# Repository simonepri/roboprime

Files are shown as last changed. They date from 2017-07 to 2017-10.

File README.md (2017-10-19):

# RoboPrime 🤖 
> Full featured 21 DOF 3D Printed Humanoid Robot based on ATmega328P chip
<p align="center">
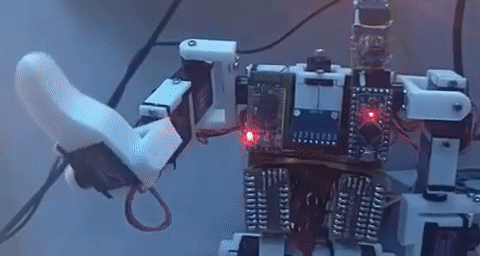
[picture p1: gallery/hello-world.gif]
RoboPrime Hello
  
</p>
Description coming soon.

### Press
The project has been featured here:
<p>
  <a href="http://explore.makerfairerome.eu/poi/Exhibit_1447" target="_blank">Maker Faire</a>
  <a href="http://www.ilmessaggero.it/pay/edicola/maker_faire_roma_14_ottobre-2001501.html" target="_blank"> Il Messagero</a>
</p>

### Gallery
Some images done during the development process:

<p>
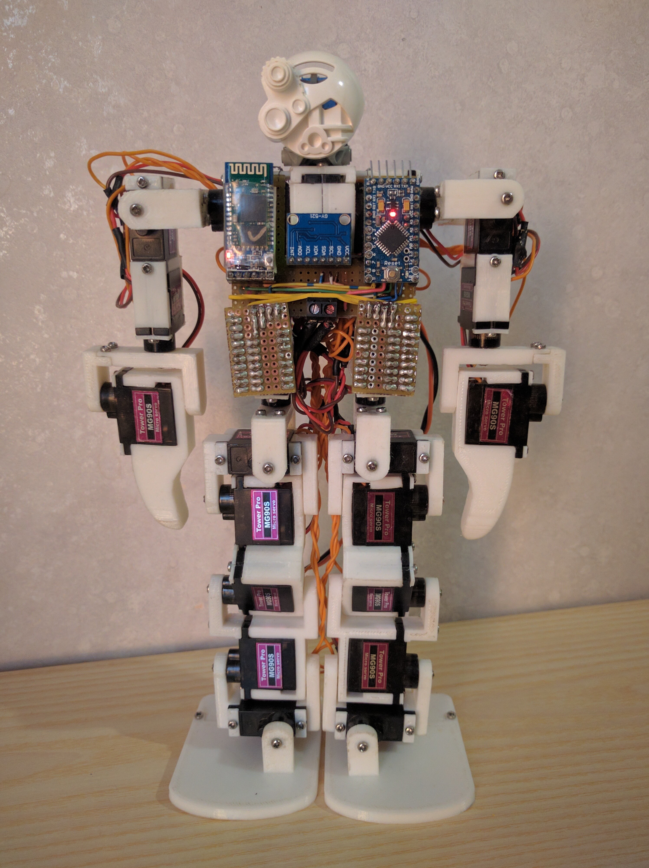
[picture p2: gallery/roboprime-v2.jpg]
RoboPrime
  
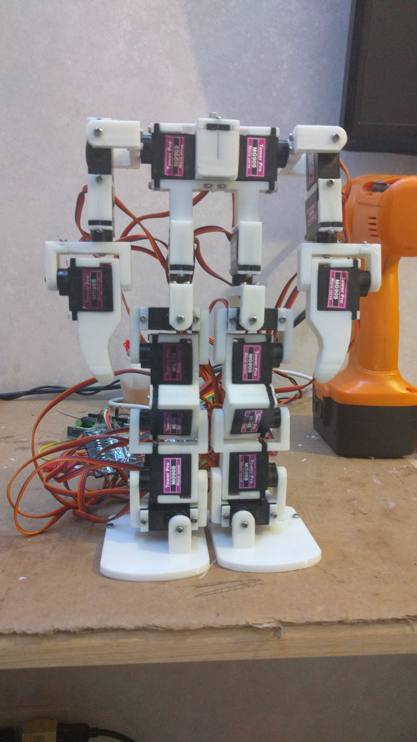
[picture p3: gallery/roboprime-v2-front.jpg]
RoboPrime
  
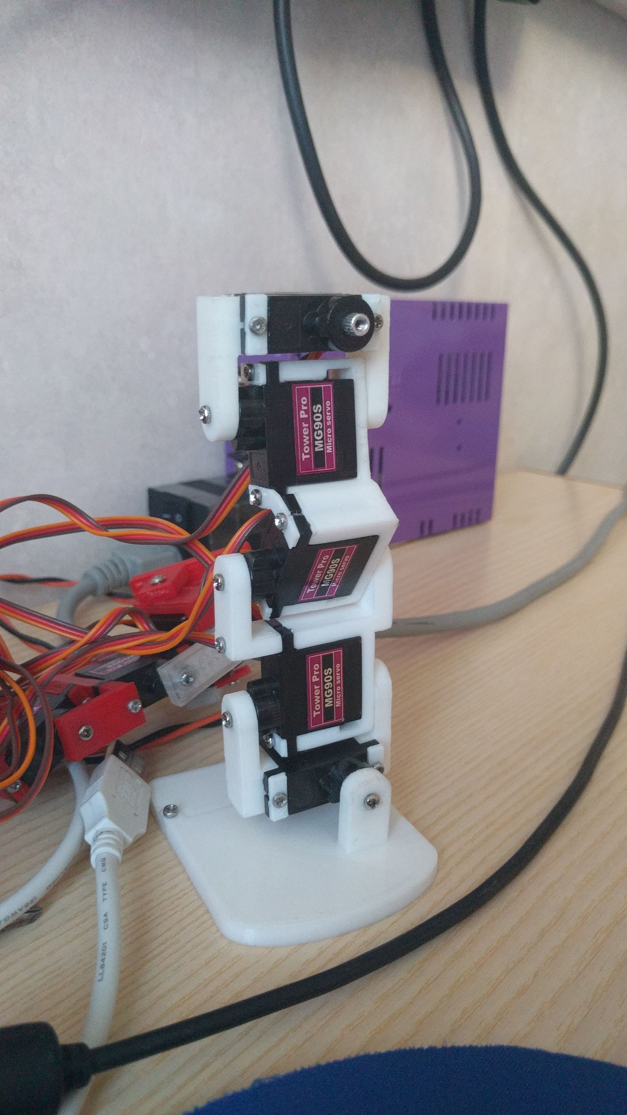
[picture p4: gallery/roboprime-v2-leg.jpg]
RoboPrime
  
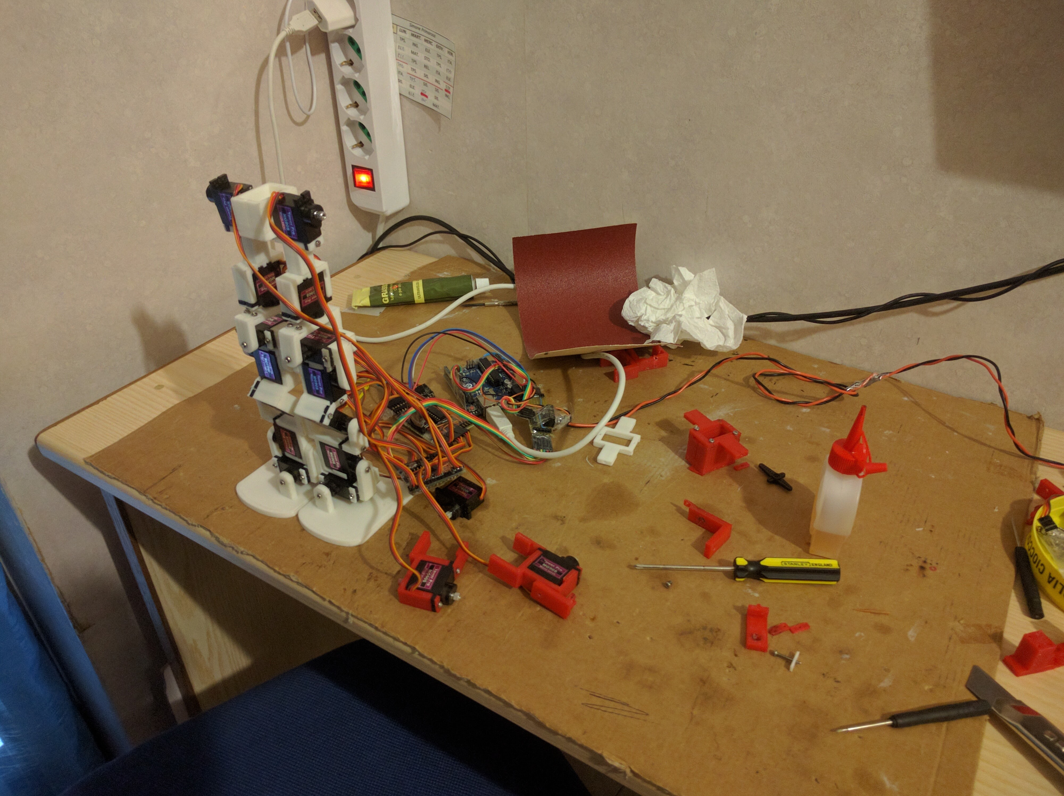
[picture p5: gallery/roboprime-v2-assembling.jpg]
RoboPrime
  
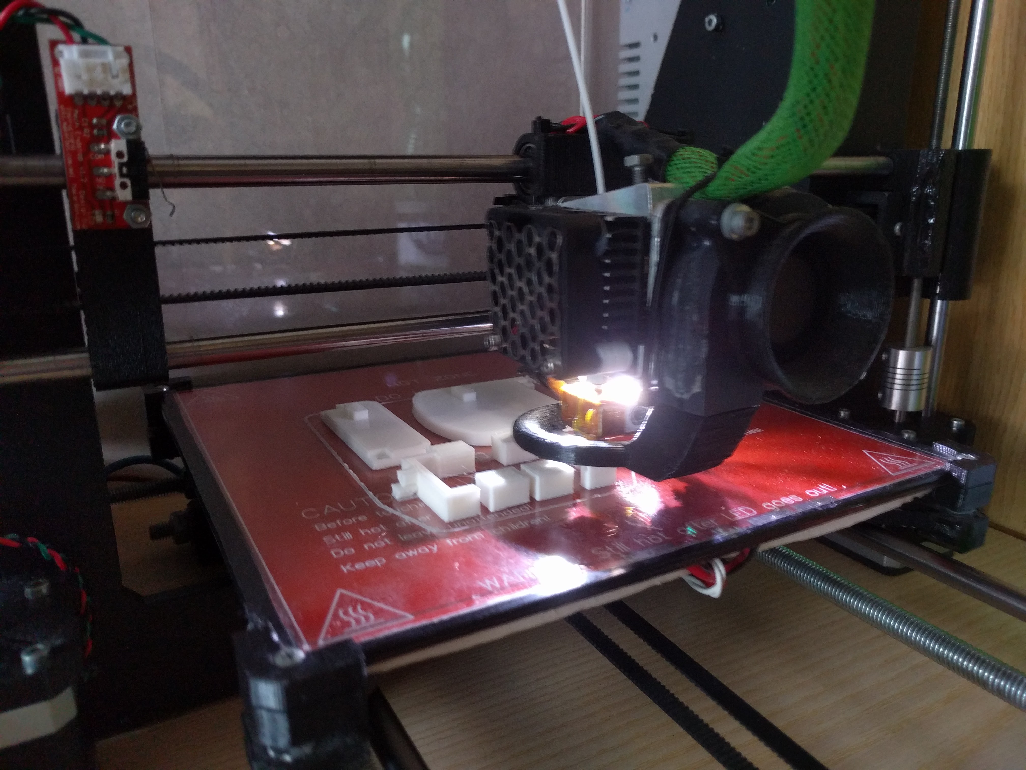
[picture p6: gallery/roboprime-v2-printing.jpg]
RoboPrime
  
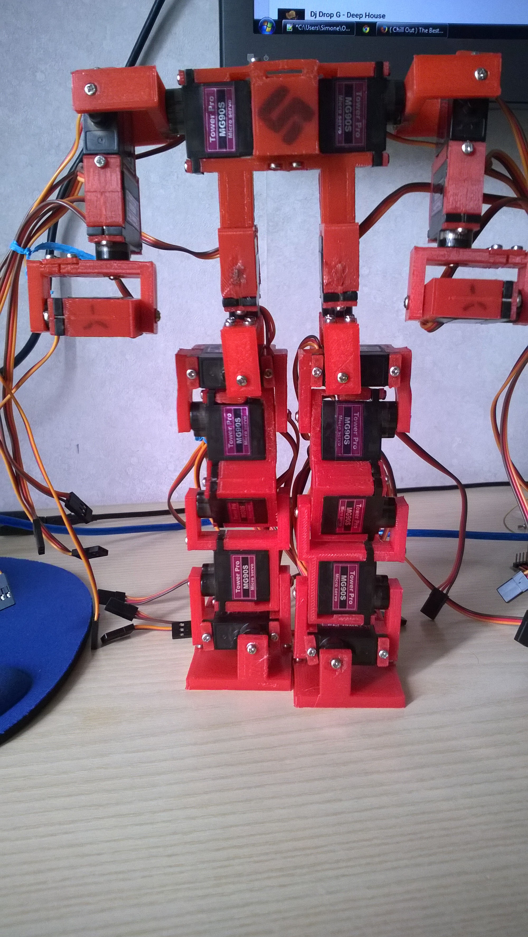
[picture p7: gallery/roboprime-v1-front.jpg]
RoboPrime
  
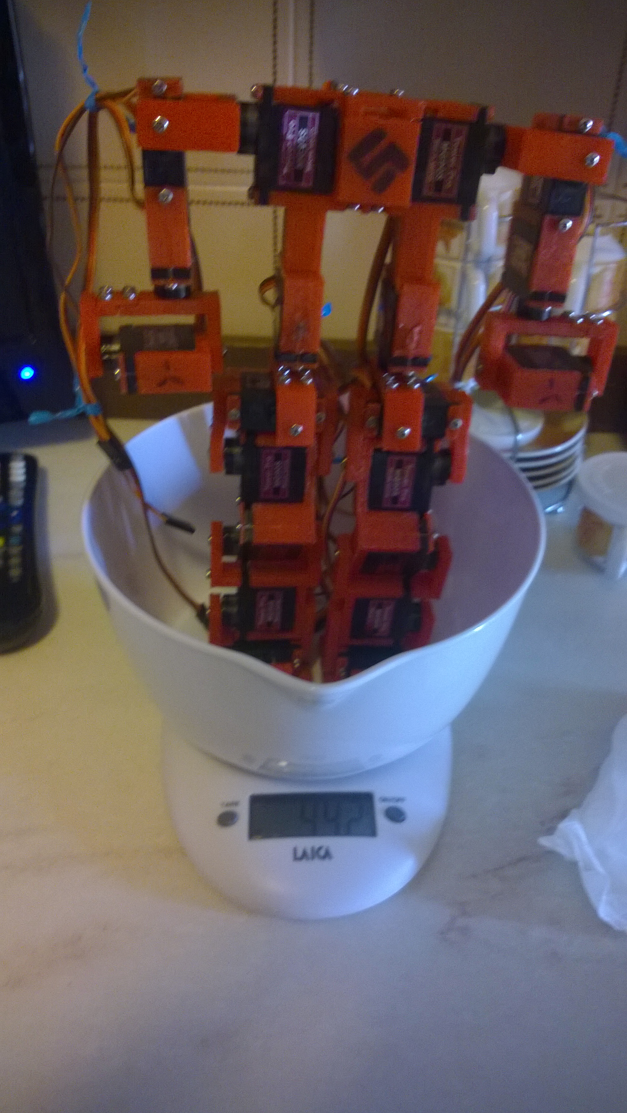
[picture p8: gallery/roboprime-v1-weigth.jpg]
RoboPrime
  
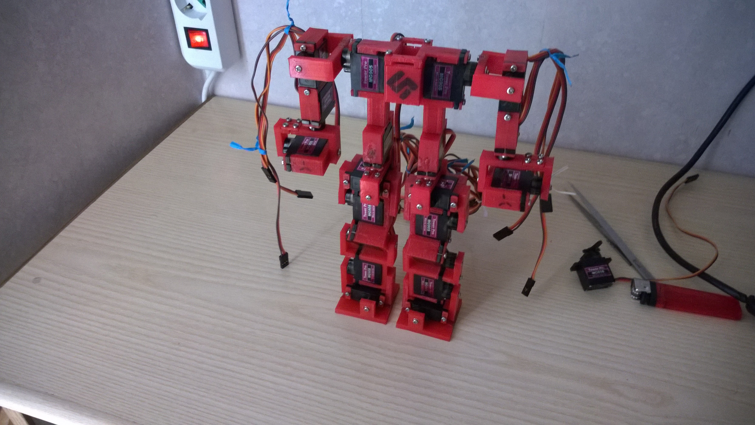
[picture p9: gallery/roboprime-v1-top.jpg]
RoboPrime
  
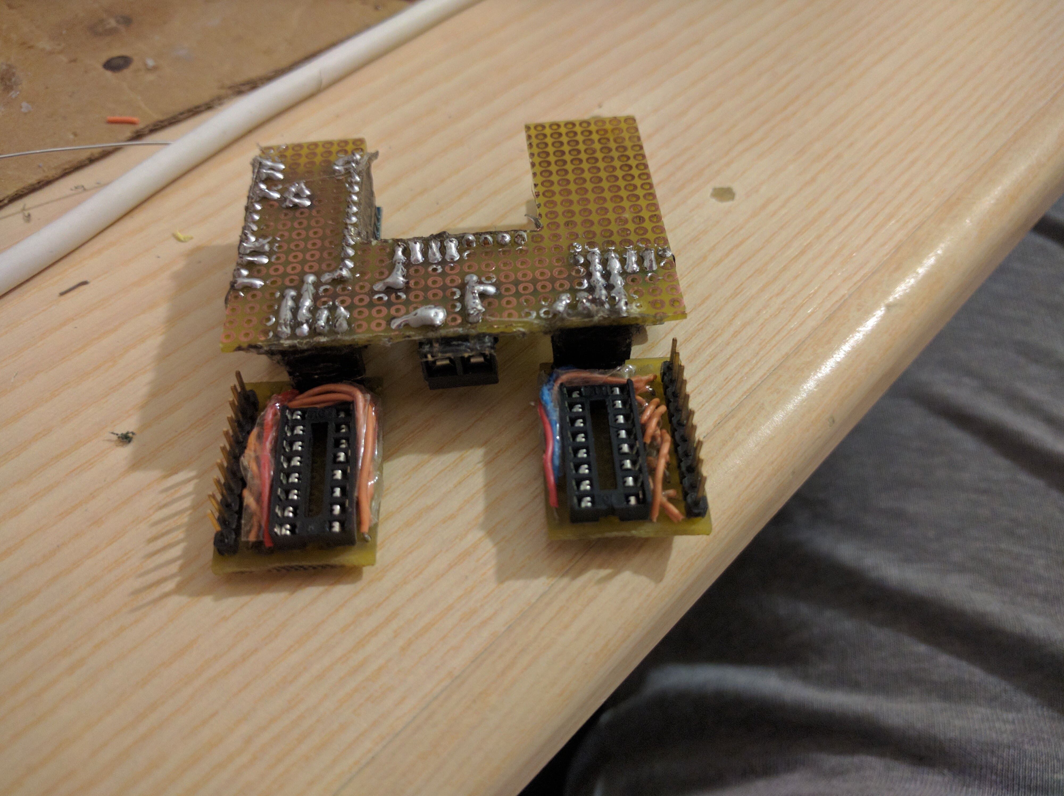
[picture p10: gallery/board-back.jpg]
  
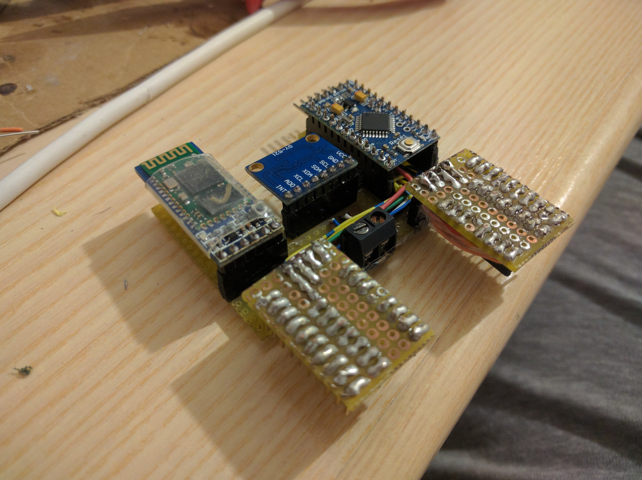
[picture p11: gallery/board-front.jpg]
  
  RoboPrime
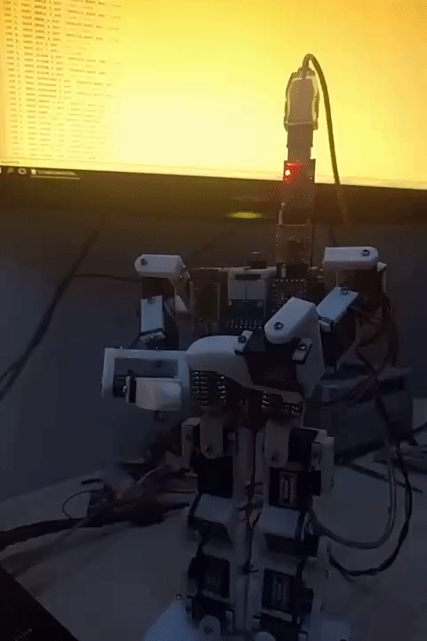
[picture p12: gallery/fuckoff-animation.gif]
  
  RoboPrime
  RoboPrime
</p>

> Click on the image to enlarge.

## Getting Started

### Hardware
The total cost is about $60-$100. Depending on where you buy the pieces.

Amount | Part
-------|---------
1 | Arduino Pro Micro (Atmega328p)
1 | HC-05 (Bluetooth)
2 | 74HC4017 (5-stage Johnson decade counter)
1 | MPU-6050 (Gyroscope + Accellerometer UNUSED)
21 | MG90S 9G (Servo motors)
2 | 5A DC-DC (Voltage step-down Used to power the servos)
1 | Ad-hoc board (See wiring section)

### Screws
Screws are used to join pieces together.

The total cost is about $15.

Amount | Size
-------|------
37 | M2 x 4mm
32 | M2 x 14mm
19 | M2 x 20mm

### 3D Models
You need to print it in ABS, since servos becomes hot after a while and can melt the plastic.

The printing cost is about $20-$30.

> SX_* models needs to be mirrored on the correct axis before the printing process.

Part | Amount | Download
-----|--------|---------
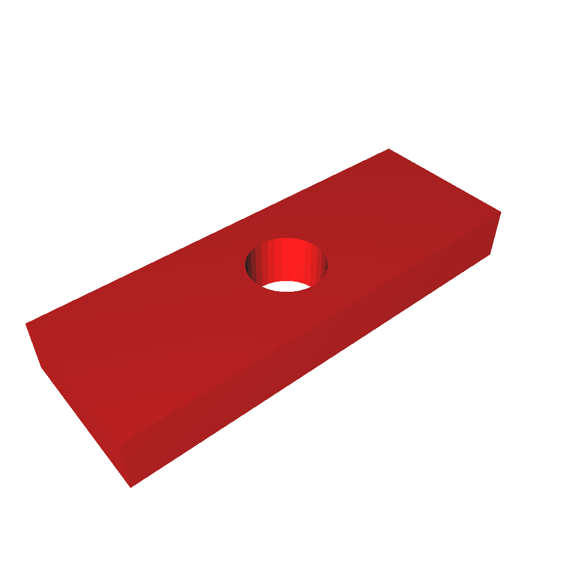
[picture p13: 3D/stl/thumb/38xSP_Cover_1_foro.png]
SP_Cover_1_foro
 | 38 | [SP_Cover_1_foro](3D/stl/38xSP_Cover_1_foro.stl)
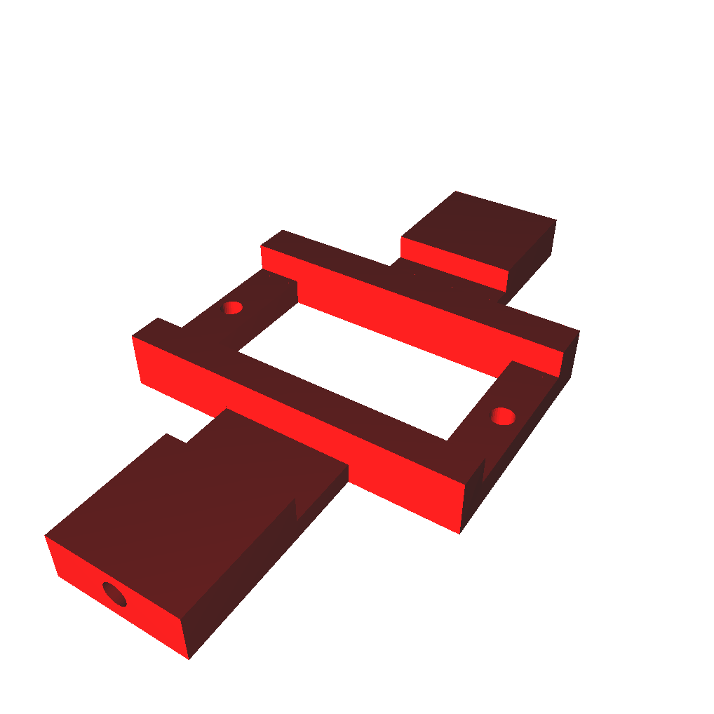
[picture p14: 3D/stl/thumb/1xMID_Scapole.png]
MID_Scapole
 | 1 | [MID_Scapole](3D/stl/1xMID_Scapole.stl)
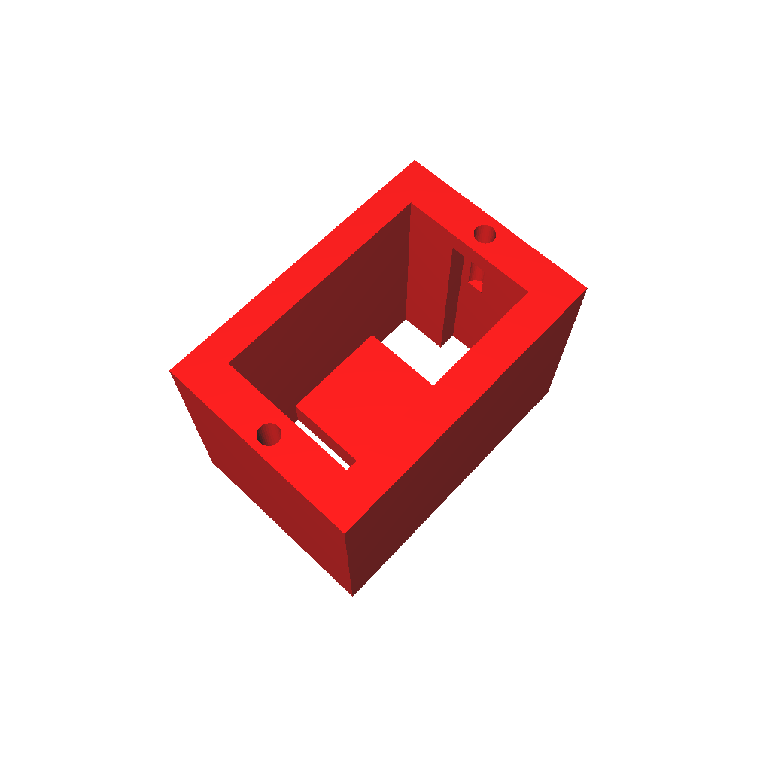
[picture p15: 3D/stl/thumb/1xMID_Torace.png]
MID_Torace
 | 1 | [MID_Torace](3D/stl/1xMID_Torace.stl)
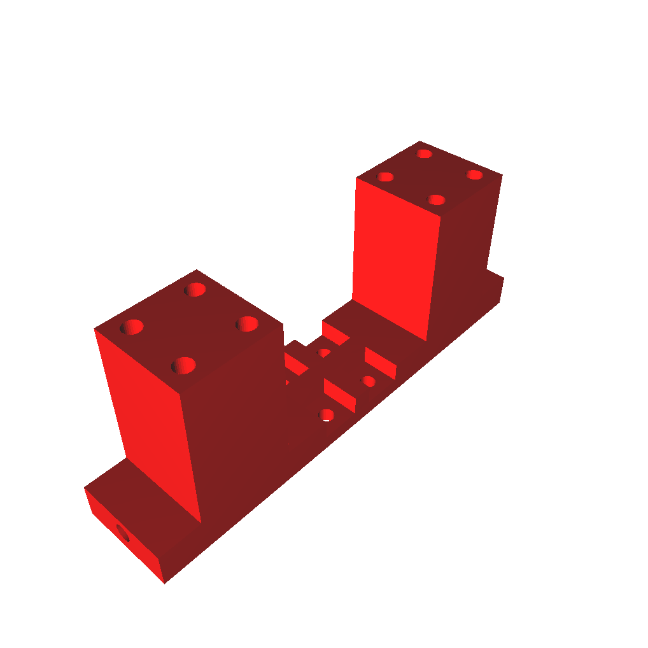
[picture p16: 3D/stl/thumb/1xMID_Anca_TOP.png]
MID_Anca_TOP
 | 1 | [MID_Anca_TOP](3D/stl/1xMID_Anca_TOP.stl)
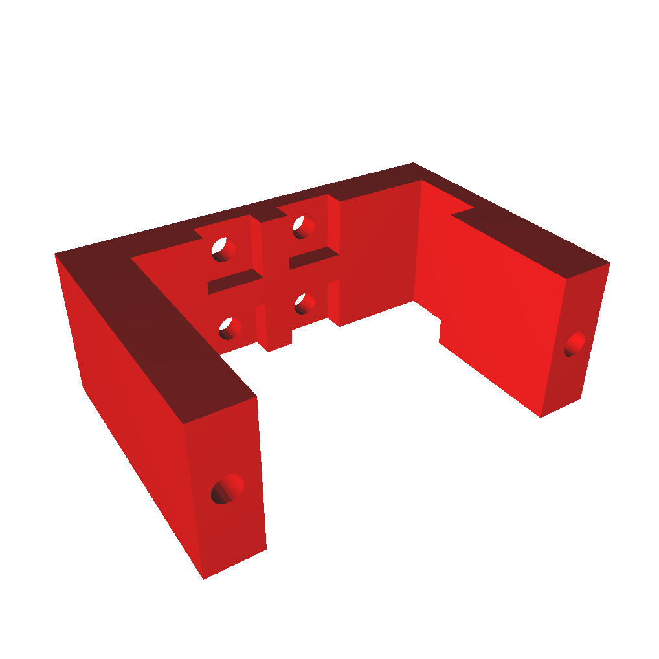
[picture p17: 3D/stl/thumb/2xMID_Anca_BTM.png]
MID_Anca_BTM
 | 2 | [MID_Anca_BTM](3D/stl/2xMID_Anca_BTM.stl)
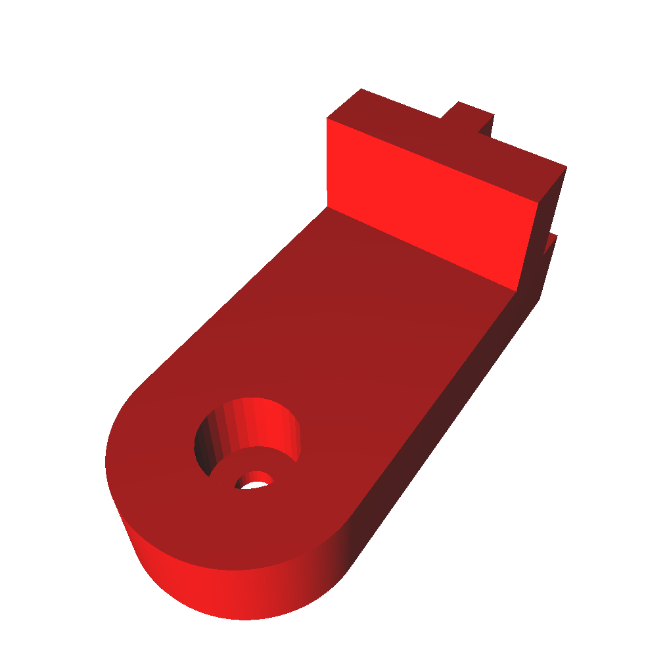
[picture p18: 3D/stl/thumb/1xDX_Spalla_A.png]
DX_Spalla_A
 | 1 | [DX_Spalla_A](3D/stl/1xDX_Spalla_A.stl)
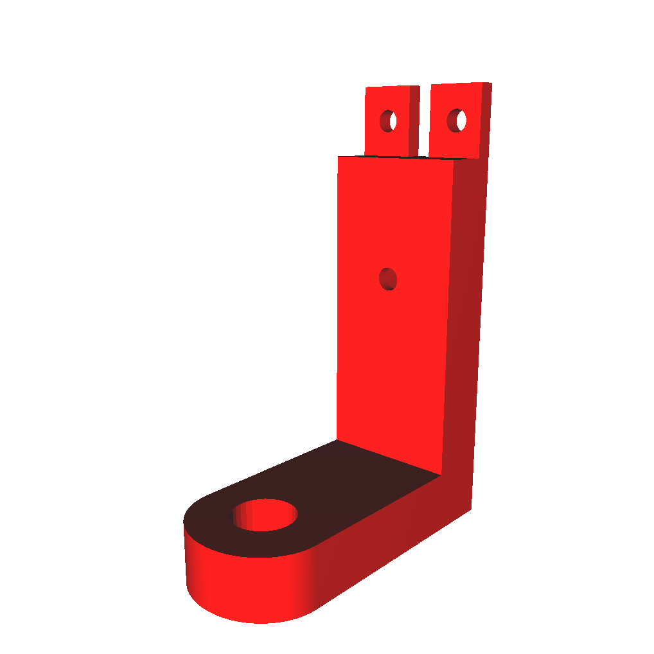
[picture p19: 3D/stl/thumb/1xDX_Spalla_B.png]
DX_Spalla_B
 | 1 | [DX_Spalla_B](3D/stl/1xDX_Spalla_B.stl)
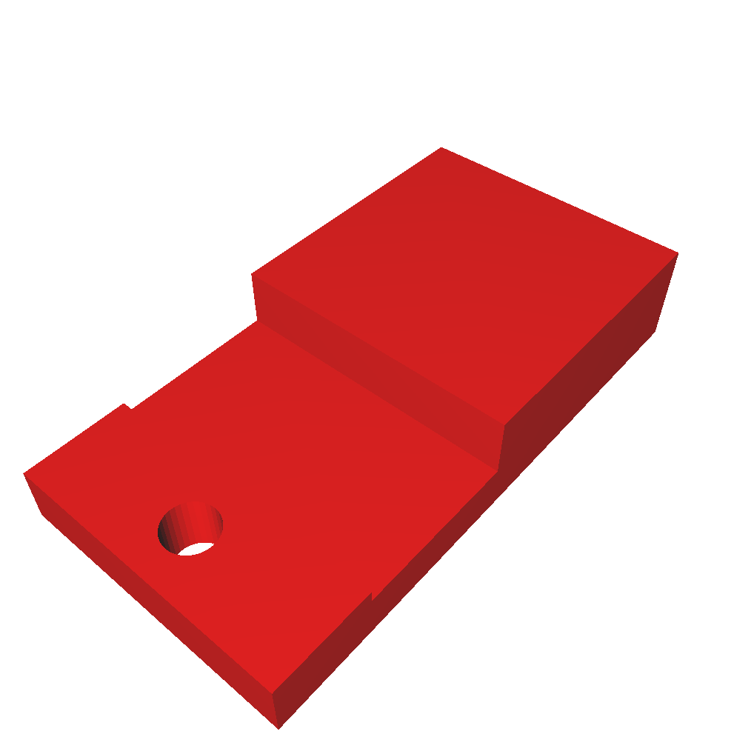
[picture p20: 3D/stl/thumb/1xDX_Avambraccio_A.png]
DX_Avambraccio_A
 | 1 | [DX_Avambraccio_A](3D/stl/1xDX_Avambraccio_A.stl)
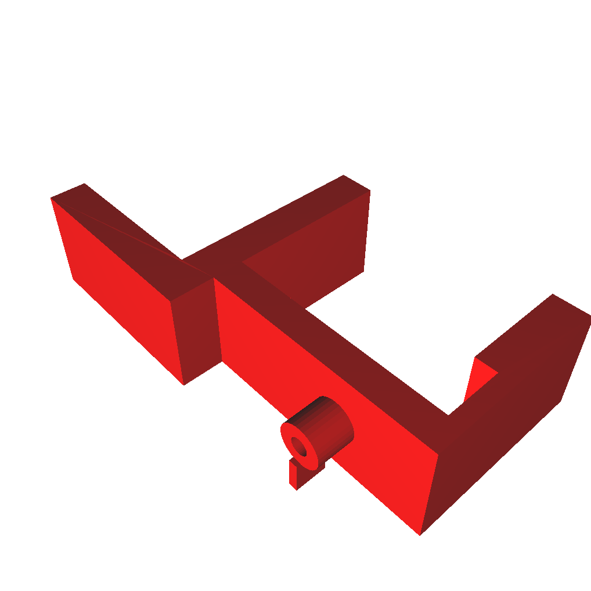
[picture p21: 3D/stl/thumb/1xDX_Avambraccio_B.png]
DX_Avambraccio_B
 | 1 | [DX_Avambraccio_B](3D/stl/1xDX_Avambraccio_B.stl)
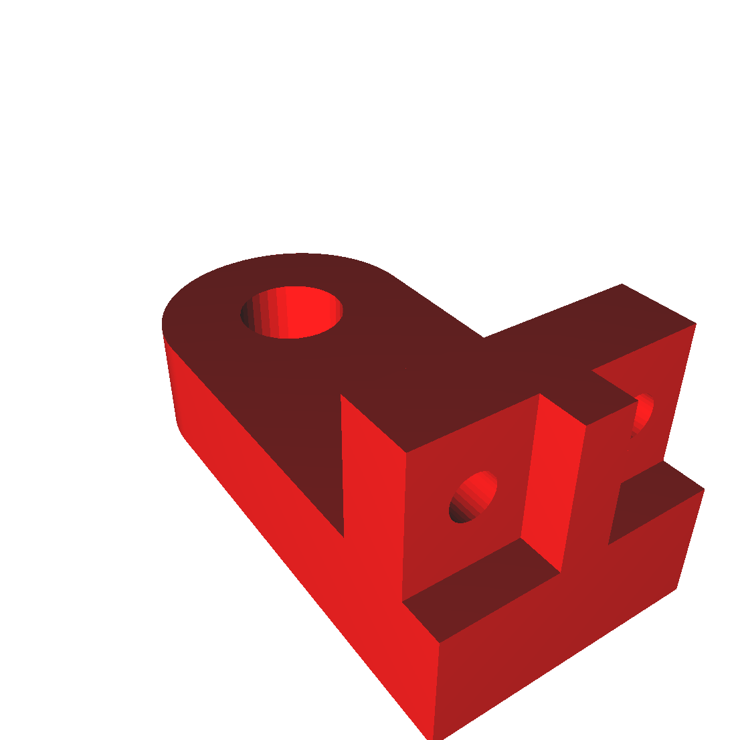
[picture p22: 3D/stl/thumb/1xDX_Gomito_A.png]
DX_Gomito_A
 | 1 | [DX_Gomito_A](3D/stl/1xDX_Gomito_A.stl)
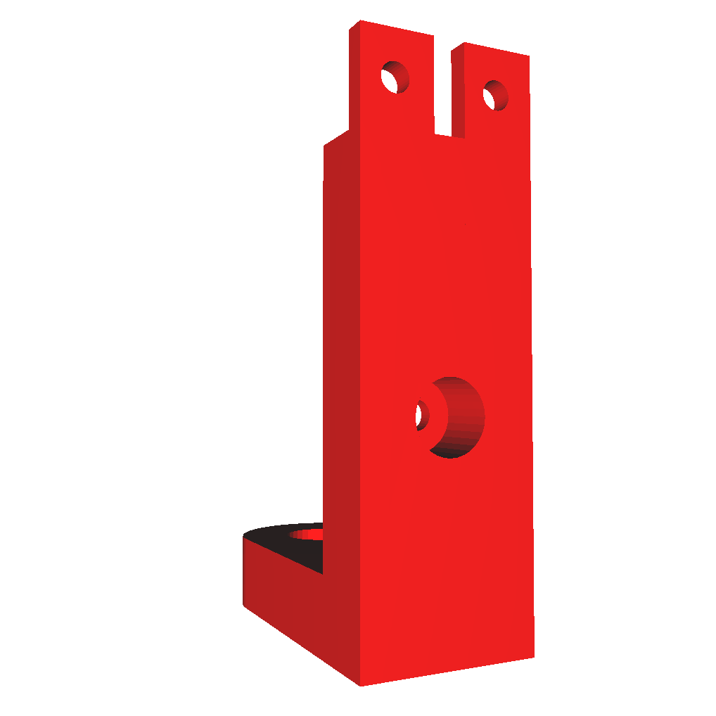
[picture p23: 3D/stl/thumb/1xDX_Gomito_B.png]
DX_Gomito_B
 | 1 | [DX_Gomito_B](3D/stl/1xDX_Gomito_B.stl)
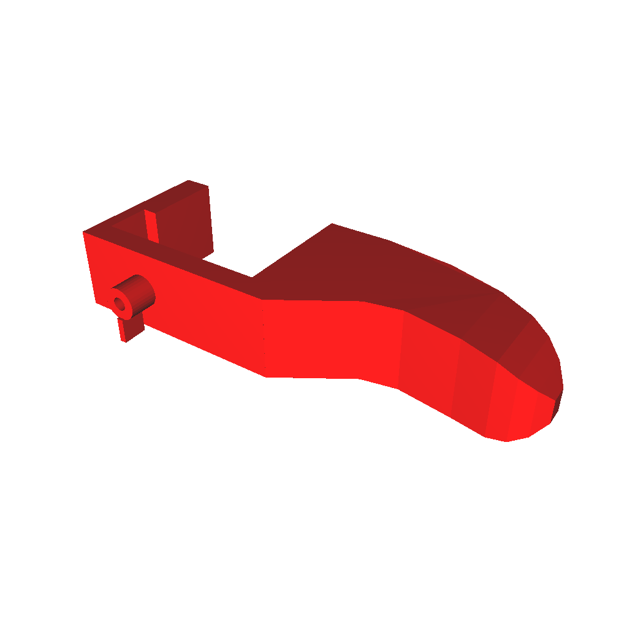
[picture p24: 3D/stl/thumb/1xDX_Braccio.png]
DX_Braccio
 | 1 | [DX_Braccio](3D/stl/1xDX_Braccio.stl)
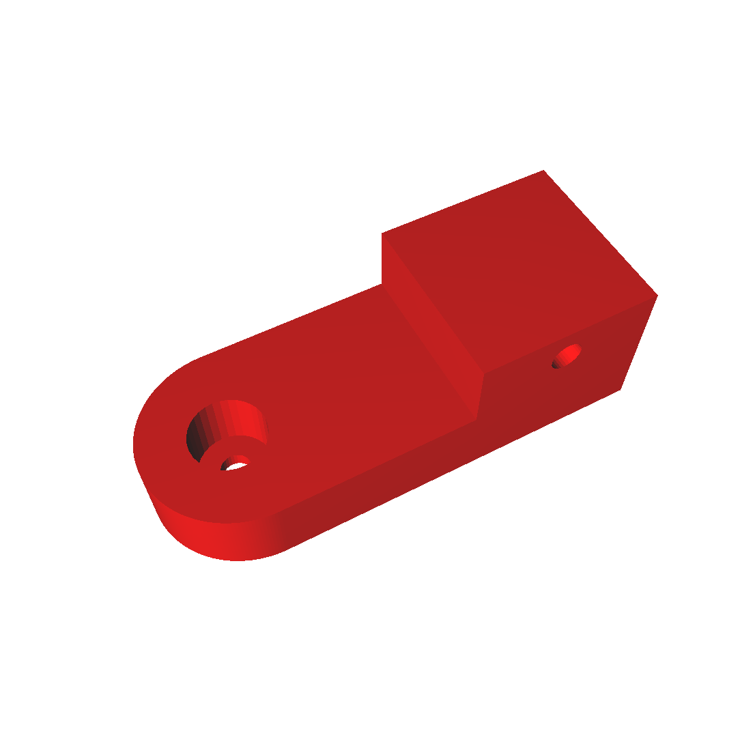
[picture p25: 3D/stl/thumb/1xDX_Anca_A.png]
DX_Anca_A
 | 1 | [DX_Anca_A](3D/stl/1xDX_Anca_A.stl)
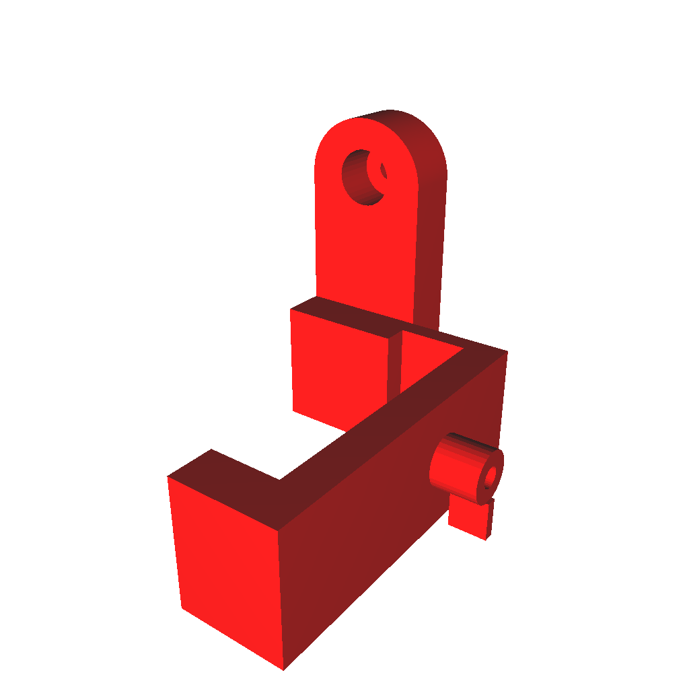
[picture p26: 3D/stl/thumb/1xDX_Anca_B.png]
DX_Anca_B
 | 1 | [DX_Anca_B](3D/stl/1xDX_Anca_B.stl)
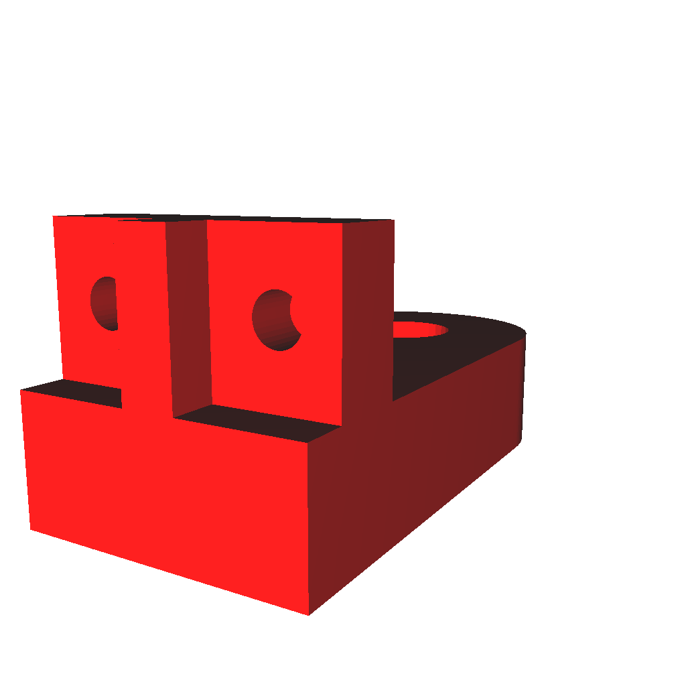
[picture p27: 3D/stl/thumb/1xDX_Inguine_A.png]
DX_Inguine_A
 | 1 | [DX_Inguine_A](3D/stl/1xDX_Inguine_A.stl)
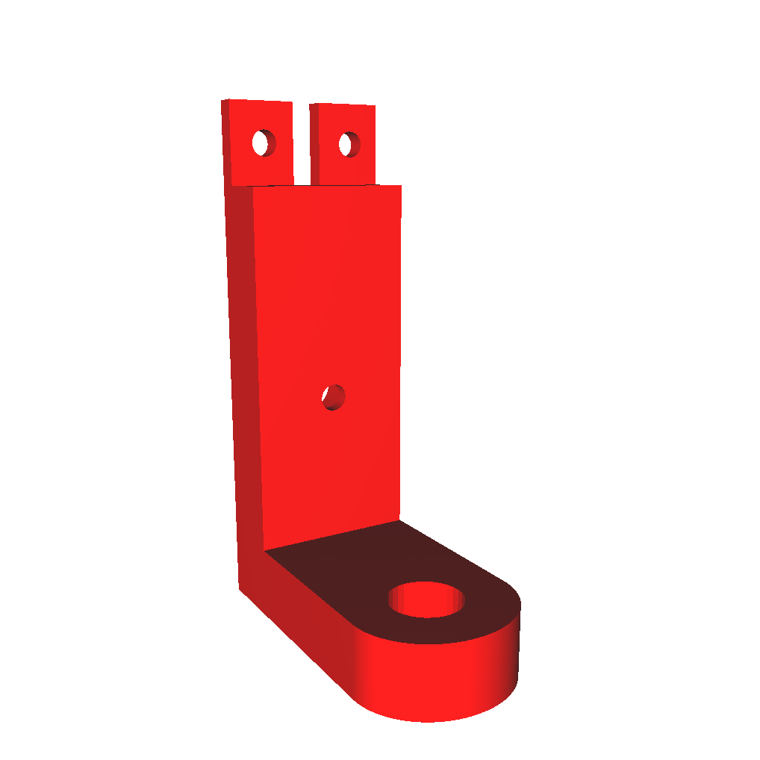
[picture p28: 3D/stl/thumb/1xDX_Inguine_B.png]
DX_Inguine_B
 | 1 | [DX_Inguine_B](3D/stl/1xDX_Inguine_B.stl)
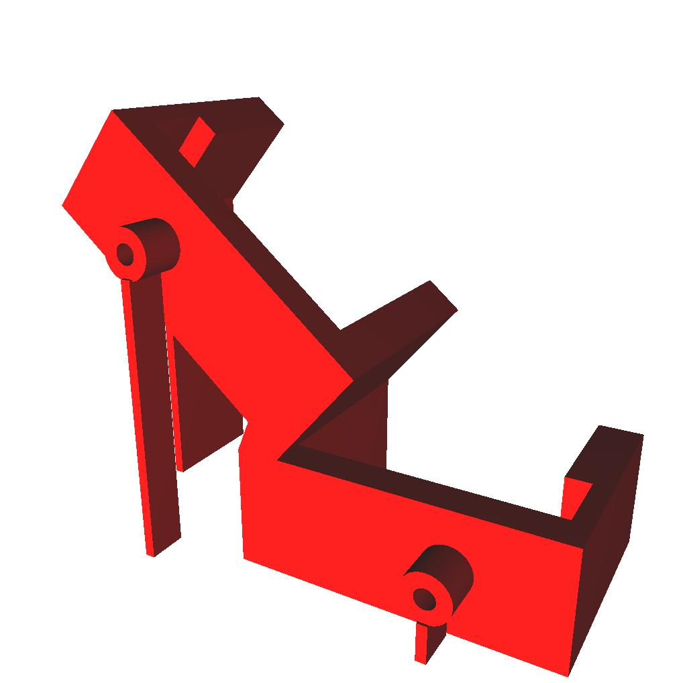
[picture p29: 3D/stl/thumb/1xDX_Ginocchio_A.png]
DX_Ginocchio_A
 | 1 | [DX_Ginocchio_A](3D/stl/1xDX_Ginocchio_A.stl)
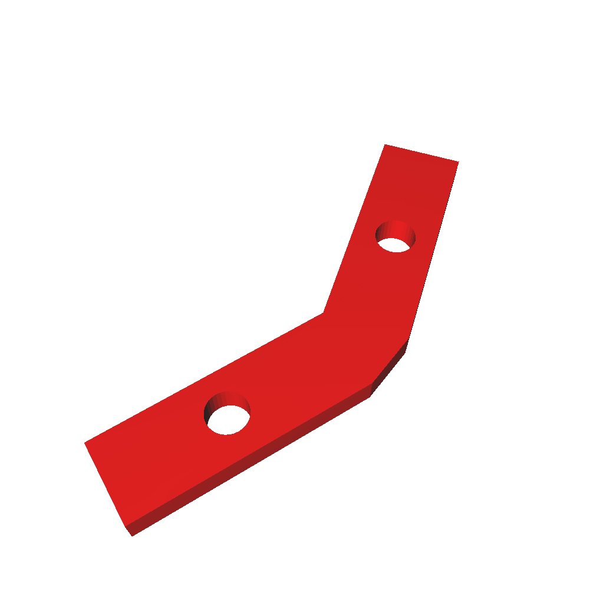
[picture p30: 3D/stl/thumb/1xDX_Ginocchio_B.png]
DX_Ginocchio_B
 | 1 | [DX_Ginocchio_B](3D/stl/1xDX_Ginocchio_B.stl)
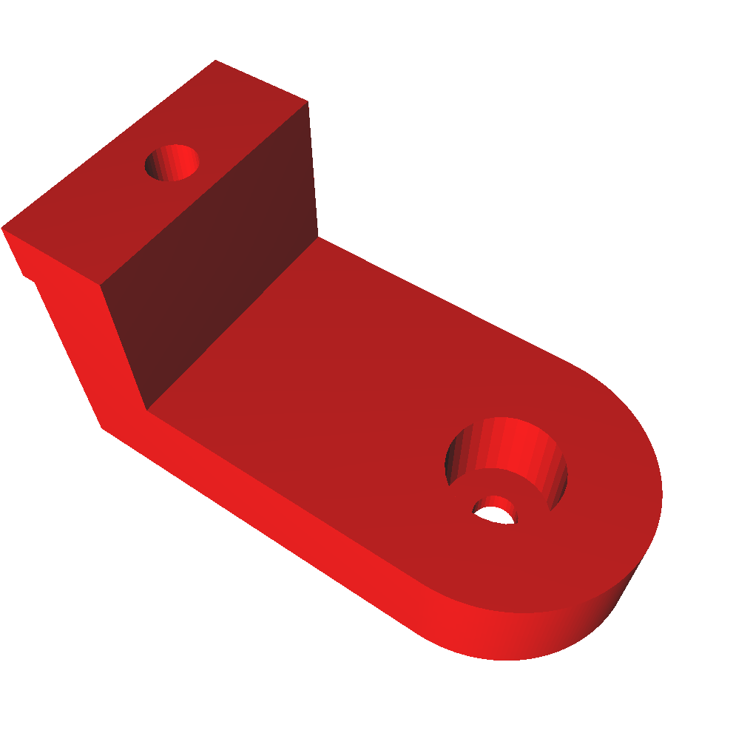
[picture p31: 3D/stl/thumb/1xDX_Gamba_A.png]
DX_Gamba_A
 | 1 | [DX_Gamba_A](3D/stl/1xDX_Gamba_A.stl)
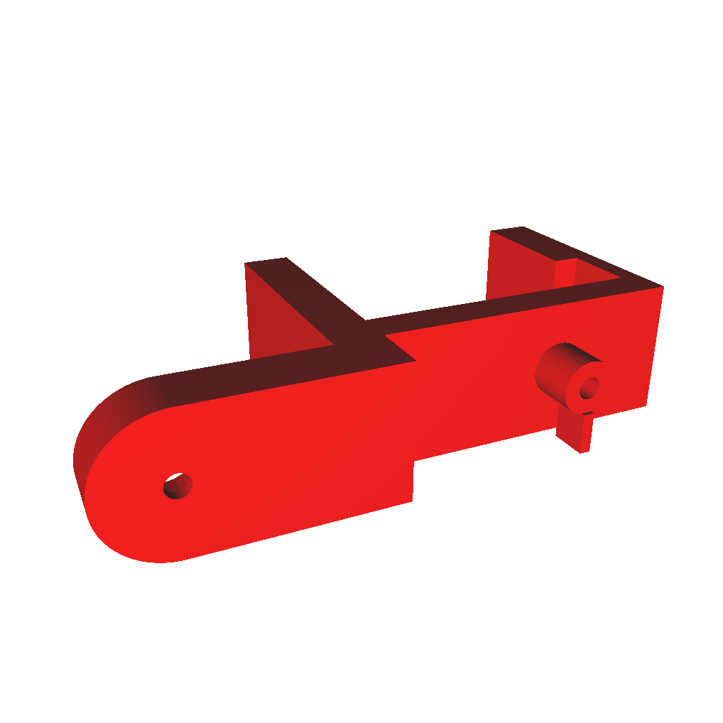
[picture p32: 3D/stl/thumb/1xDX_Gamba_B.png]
DX_Gamba_B
 | 1 | [DX_Gamba_B](3D/stl/1xDX_Gamba_B.stl)
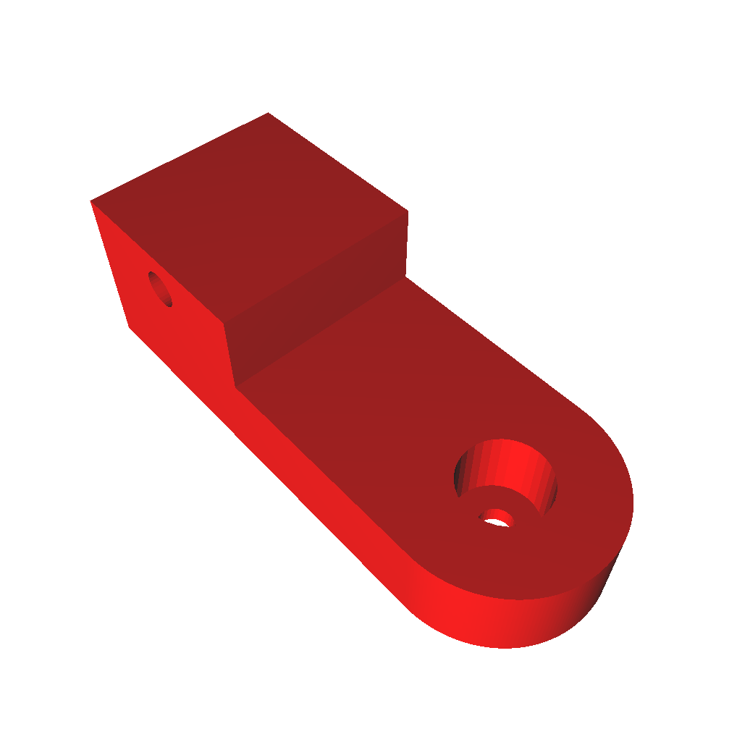
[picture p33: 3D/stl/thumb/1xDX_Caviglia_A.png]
DX_Caviglia_A
 | 1 | [DX_Caviglia_A](3D/stl/1xDX_Caviglia_A.stl)
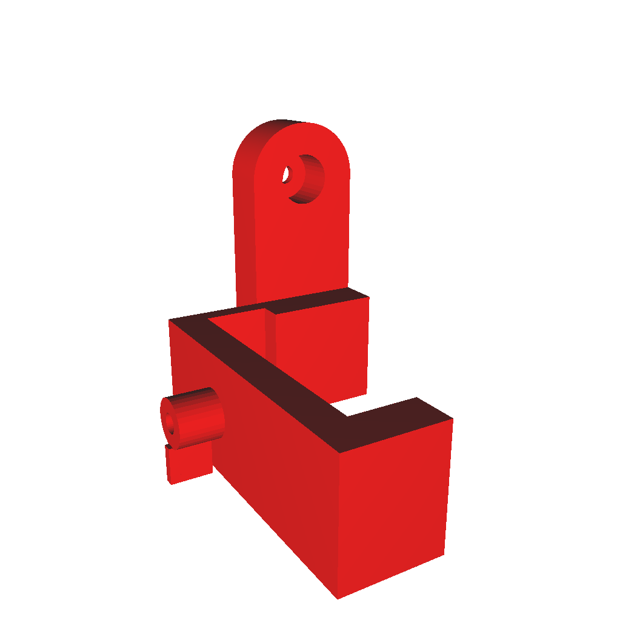
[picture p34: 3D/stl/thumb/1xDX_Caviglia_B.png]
DX_Caviglia_B
 | 1 | [DX_Caviglia_B](3D/stl/1xDX_Caviglia_B.stl)
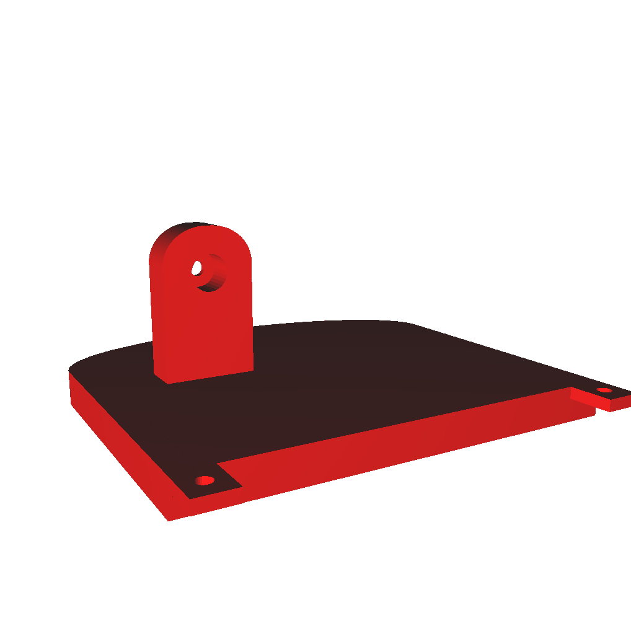
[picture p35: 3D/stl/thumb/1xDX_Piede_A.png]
DX_Piede_A
 | 1 | [DX_Piede_A](3D/stl/1xDX_Piede_A.stl)
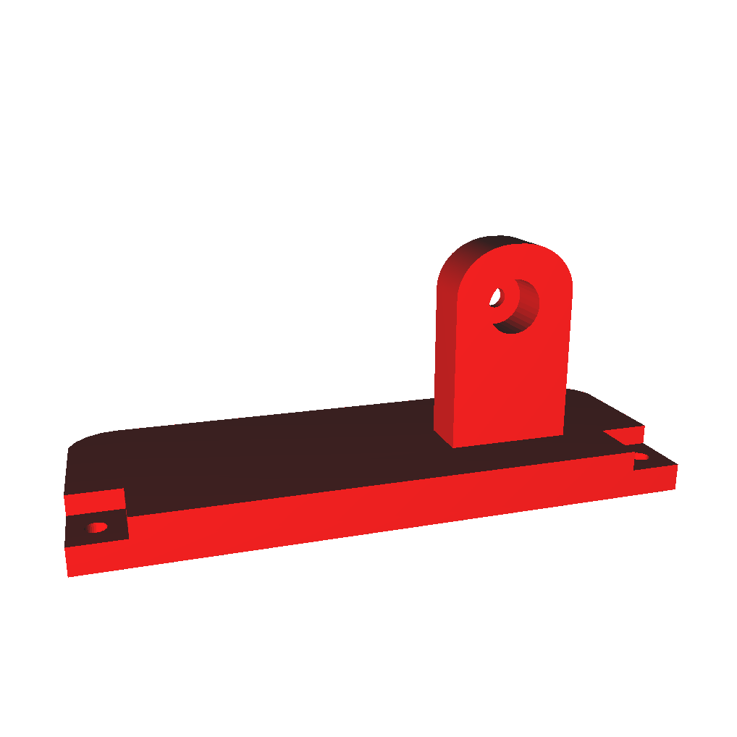
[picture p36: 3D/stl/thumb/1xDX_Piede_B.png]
DX_Piede_B
 | 1 | [DX_Piede_B](3D/stl/1xDX_Piede_B.stl)
SX_Spalla_A | 1 | [SX_Spalla_A](3D/stl/1xDX_Spalla_A.stl)
SX_Spalla_B | 1 | [SX_Spalla_B](3D/stl/1xDX_Spalla_B.stl)
SX_Avambraccio_A | 1 | [SX_Avambraccio_A](3D/stl/1xDX_Avambraccio_A.stl)
SX_Avambraccio_B | 1 | [SX_Avambraccio_B](3D/stl/1xDX_Avambraccio_B.stl)
SX_Gomito_A | 1 | [SX_Gomito_A](3D/stl/1xDX_Gomito_A.stl)
SX_Gomito_B | 1 | [SX_Gomito_B](3D/stl/1xDX_Gomito_B.stl)
SX_Braccio | 1 | [SX_Braccio](3D/stl/1xDX_Braccio.stl)
SX_Anca_A | 1 | [SX_Anca_A](3D/stl/1xDX_Anca_A.stl)
SX_Anca_B | 1 | [SX_Anca_B](3D/stl/1xDX_Anca_B.stl)
SX_Inguine_A | 1 | [SX_Inguine_A](3D/stl/1xDX_Inguine_A.stl)
SX_Inguine_B | 1 | [SX_Inguine_B](3D/stl/1xDX_Inguine_B.stl)
SX_Ginocchio_A | 1 | [SX_Ginocchio_A](3D/stl/1xDX_Ginocchio_A.stl)
SX_Ginocchio_B | 1 | [SX_Ginocchio_B](3D/stl/1xDX_Ginocchio_B.stl)
SX_Gamba_A | 1 | [SX_Gamba_A](3D/stl/1xDX_Gamba_A.stl)
SX_Gamba_B | 1 | [SX_Gamba_B](3D/stl/1xDX_Gamba_B.stl)
SX_Caviglia_A | 1 | [SX_Caviglia_A](3D/stl/1xDX_Caviglia_A.stl)
SX_Caviglia_B | 1 | [SX_Caviglia_B](3D/stl/1xDX_Caviglia_B.stl)
SX_Piede_A | 1 | [SX_Piede_A](3D/stl/1xDX_Piede_A.stl)
SX_Piede_B | 1 | [SX_Piede_B](3D/stl/1xDX_Piede_B.stl)

### Wiring
Schematics are contained in the `schematics` folder.
RoboPrime fritzing

### Firmware
The firmware is contained in the `firmware` folder and can be compiled and uploaded to the board thanks to the Arduino IDE.

Firmware size

## Usage

### Commands
The firmware allows you to fully control the robot through bluetooth in order to make complex things.
Those are the commands implemented that can be sended through the serial protocol.

Name | Syntax | Parameters | Description
-----|--------|------------|------------
S0 | `S0 Ri`<br>or<br>`S0 Li` | **i** = index[0-9] (optional) | Move a servo to its default position.<br>If no index is passed all servos will be reset.
S1 | `S1 Ri Ad`<br>or<br>`S1 Li Ad` | **i** = index[0-9]<br>**d** = angle[0-1800] | Move a servo to a specific angle.<br>The value 0 corresponds to 0° and <br>the value 1800 corresponds to 180°.
S2 | `S1 Ri Ad Tm`<br>or<br>`S1 Li Ad Tm` | **i** = index[0-9]<br>**d** = angle[0-1800]<br>**m** = duration[ms] | Move a servo to a specific angle gradually by <br>sweeping it for a specific amount of time.
S3 | `S3 An Ds Tm` | **n** = anim idx[0-10]<br>**s** = space[cm]<br>**m** = duration[ms] | Apply a specific animation.<br>`space` and `duration` are unused at the moment <br>but are supposed to be used as parameters for <br>certain animations. See animations section for <br>the list of animations available.
Q0 | `Q0 Ri Ad`<br>or<br>`Q0 Ri Ad` | **i** = index[0-9]<br>**d** = angle[0-1800] | Similar to `S1`, but the movement is added to <br>the movements queue. If the angle value is 0 <br>a pause will be planned instead.<br>(A pause will make the next planned <br>movement, on the same motor index, hang until <br>the pause is not ended)<br>This is used in order to plan complex <br>synchronized movements. (E.g. Animations)
C0 | `Ri Wp`<br>or<br>`Li Wp` | **i** = index[0-9]<br>**p** = pulse width[us] | Sets a specific pulse width to a specific <br>motor for calibration purposes.

### Animations

The firmware contains some basic animations hardcoded inside it:

Id | Name | Status
---|------|-------
0  | Forward walk.                         | WIP
1  | Backward walk.                        | NO
2  | Side walk to right.                   | NO
3  | Side walk to left.                    | NO
4  | Clockwise standstill rotation.        | NO
5  | Counterclockwise standstill rotation. | NO
6  | Clockwise curved walk.                | NO
7  | Counterclockwise curved walk.         | NO
8  | Sit down.                             | DONE
9  | Hello.                                | DONE
10 | Fuck off.                             | DONE

## Project Analysis
This document was written for my high-school exam in order to give to the professors some basic knowledge to make them understand how the project works.

Unfortunately it's written in Italian 🇮🇹

[The document is available here](https://goo.gl/ZiD9bK)

## Authors
* **Simone Primarosa** - [simonepri](https://github.com/simonepri)

See also the list of [contributors](https://github.com/simonepri/roboprime/contributors) who participated in this project.

## License
This project is licensed under the GPL-3.0 License - see the [LICENSE](LICENSE) file for details.

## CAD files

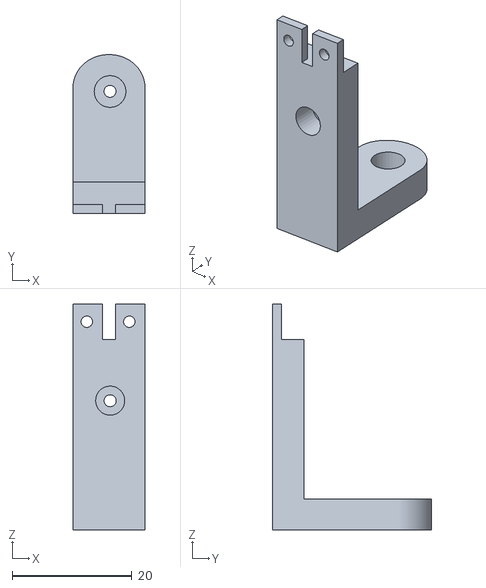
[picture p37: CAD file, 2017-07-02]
3D/stl/1xDX_Spalla_B.stl
12.0 x 26.5 x 37.7

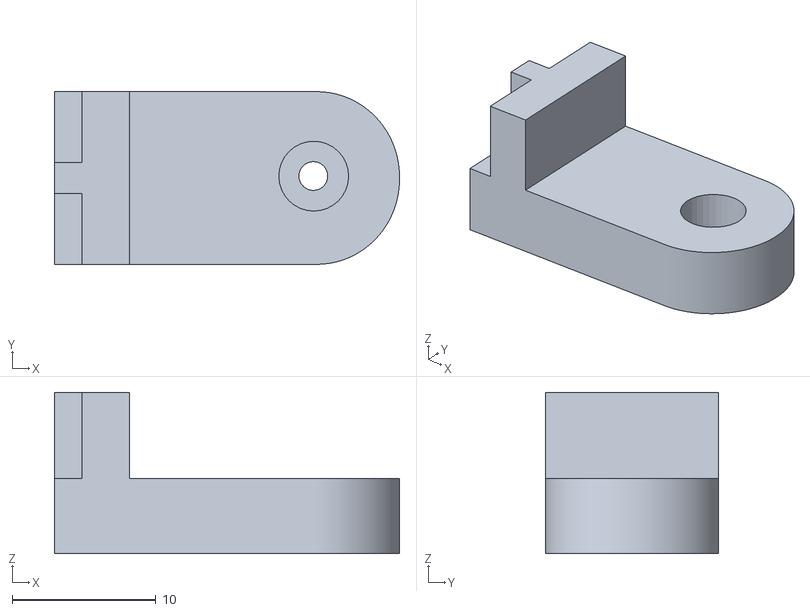
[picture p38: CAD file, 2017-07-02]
3D/stl/1xDX_Inguine_A.stl
24.0 x 12.0 x 11.2

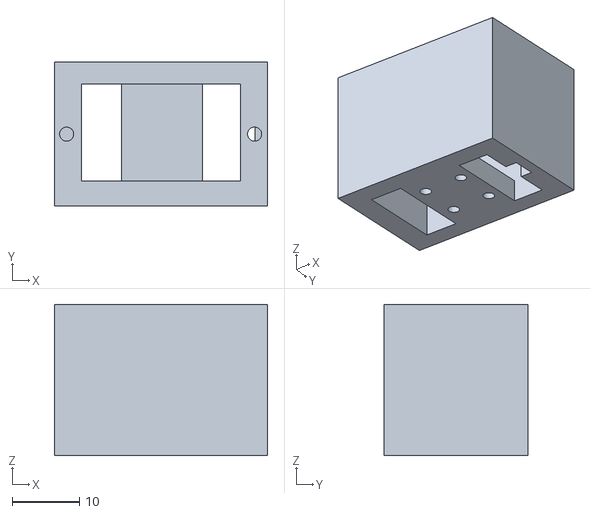
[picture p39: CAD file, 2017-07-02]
3D/stl/1xMID_Torace.stl
31.6 x 21.3 x 22.4

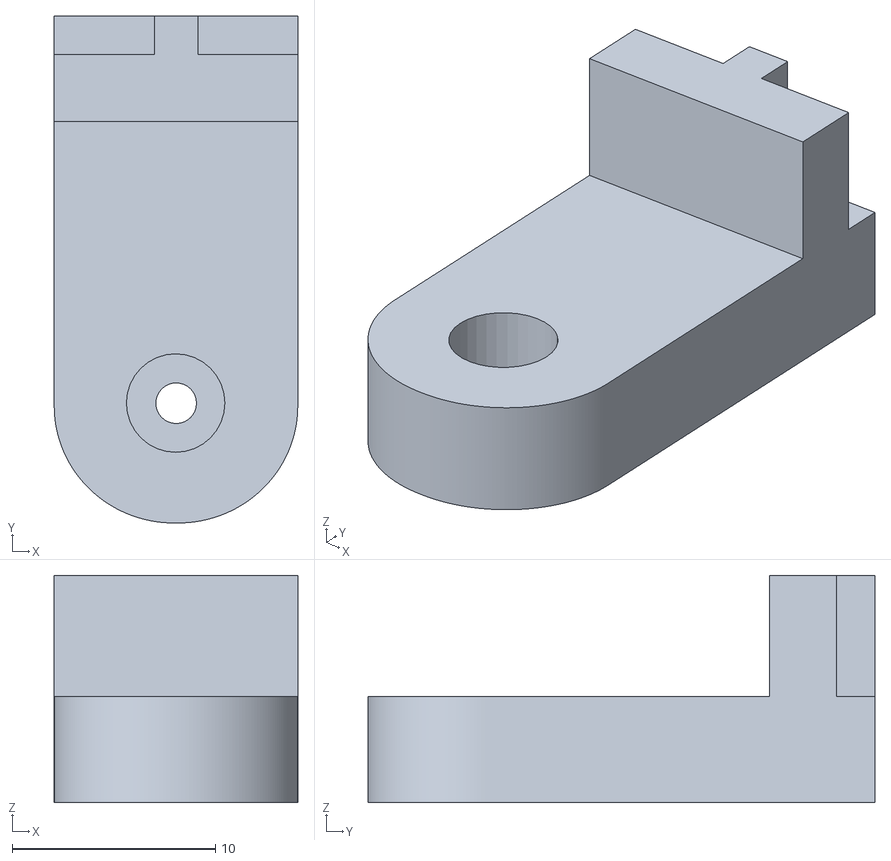
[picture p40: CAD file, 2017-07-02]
3D/stl/1xDX_Gomito_A.stl
12.0 x 25.0 x 11.2

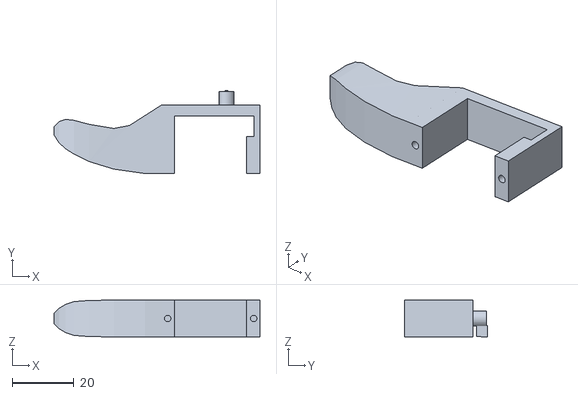
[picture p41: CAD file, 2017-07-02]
3D/stl/1xDX_Braccio.stl
66.9 x 27.0 x 12.0

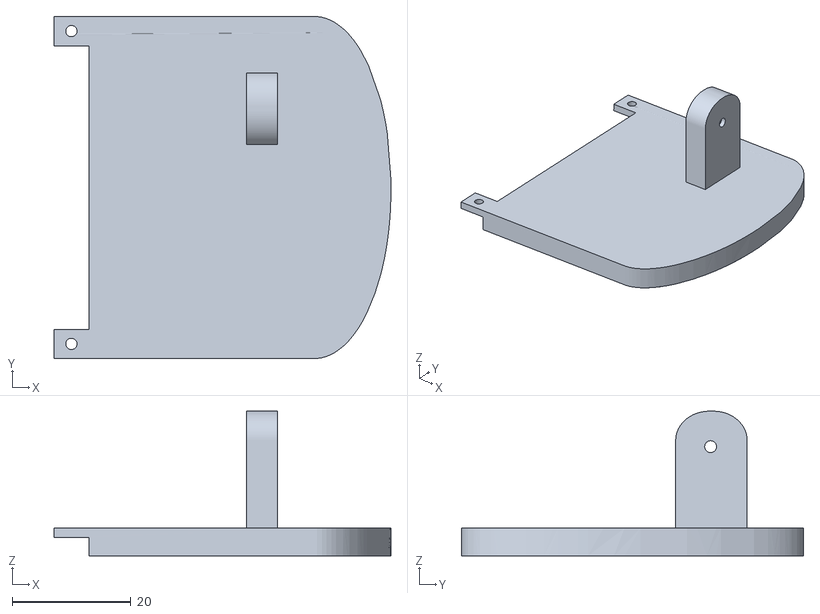
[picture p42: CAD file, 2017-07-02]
3D/stl/1xDX_Piede_A.stl
56.6 x 57.5 x 24.3

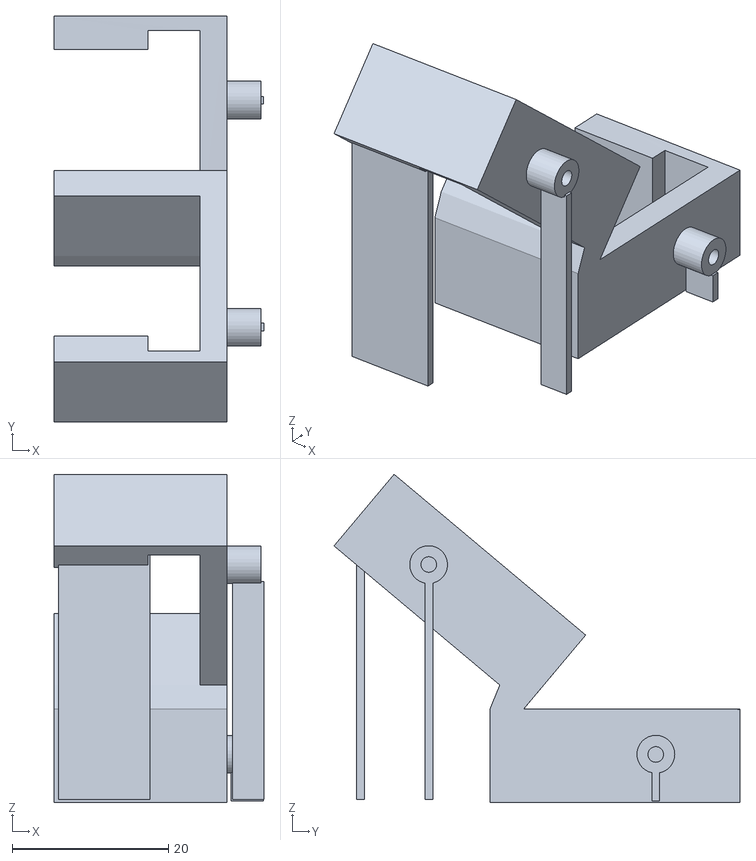
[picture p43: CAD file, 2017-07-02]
3D/stl/1xDX_Ginocchio_A.stl
26.9 x 52.0 x 42.1

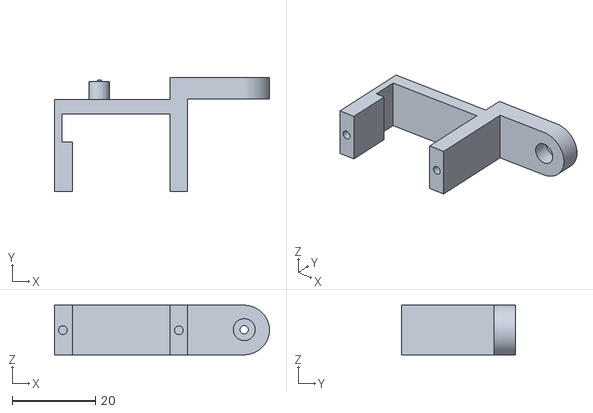
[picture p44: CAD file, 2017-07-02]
3D/stl/1xDX_Gamba_B.stl
51.8 x 27.5 x 12.0

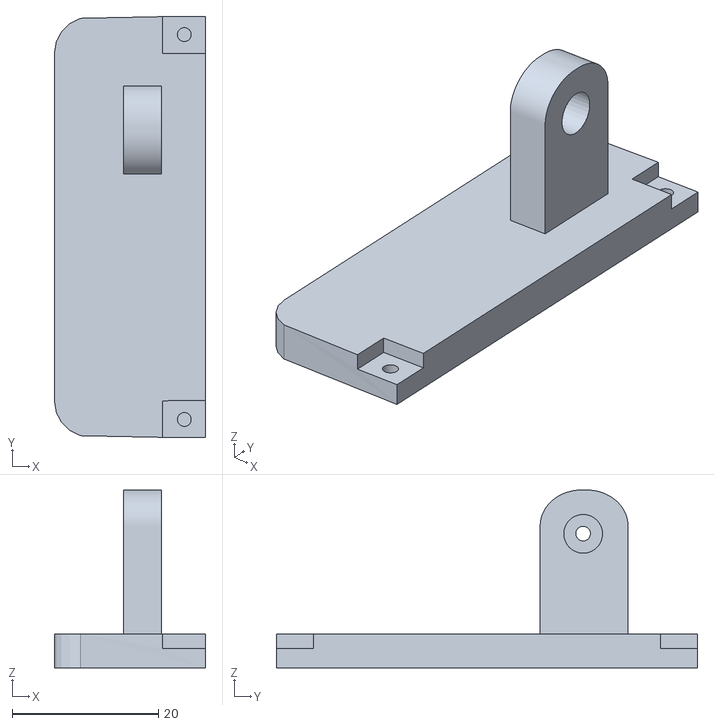
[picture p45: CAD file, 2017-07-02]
3D/stl/1xDX_Piede_B.stl
20.6 x 57.5 x 24.3

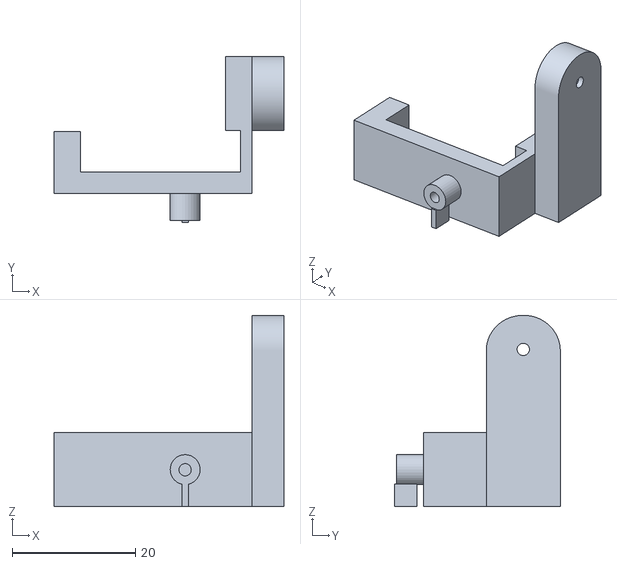
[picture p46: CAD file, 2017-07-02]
3D/stl/1xDX_Anca_B.stl
37.3 x 26.8 x 31.0

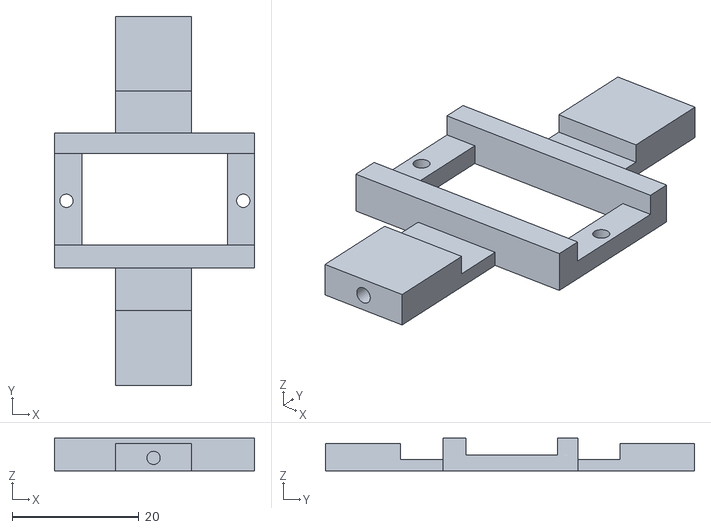
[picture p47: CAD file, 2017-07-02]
3D/stl/1xMID_Scapole.stl
31.6 x 58.2 x 5.20

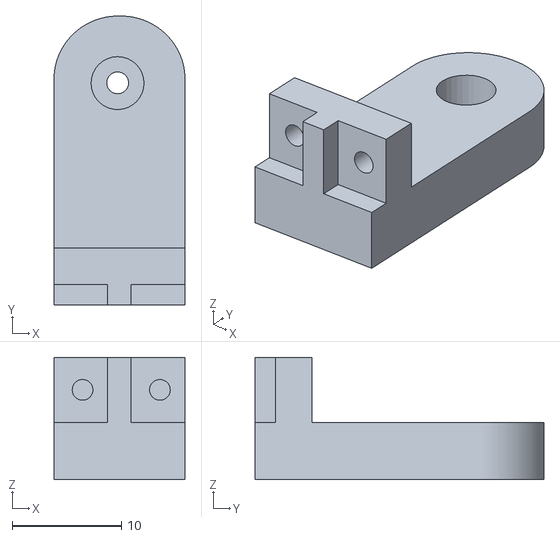
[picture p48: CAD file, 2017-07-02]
3D/stl/1xDX_Spalla_A.stl
12.0 x 26.5 x 11.2

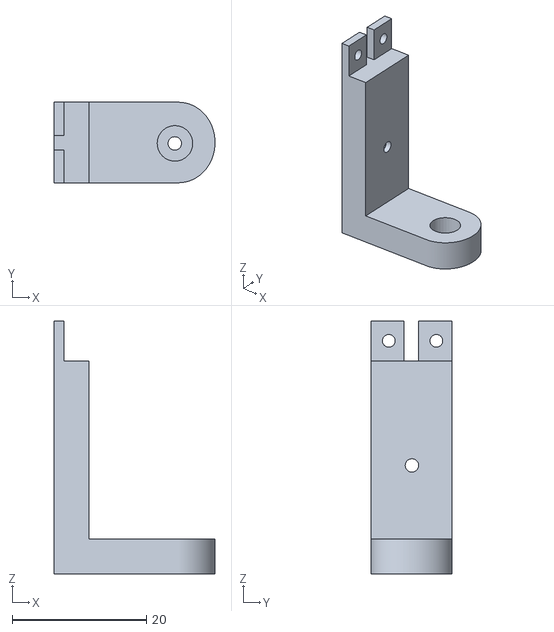
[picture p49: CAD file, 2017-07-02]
3D/stl/1xDX_Inguine_B.stl
24.0 x 12.0 x 37.7

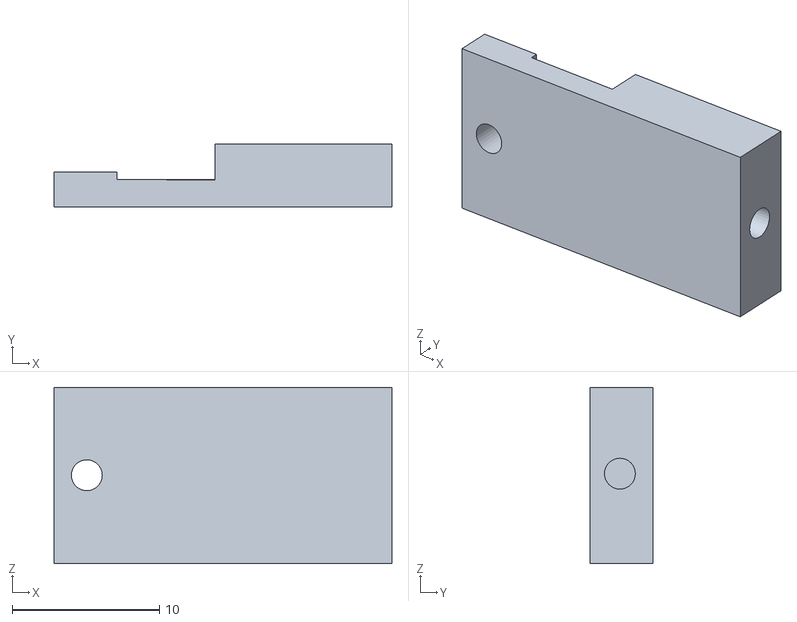
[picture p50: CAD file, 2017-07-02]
3D/stl/1xDX_Avambraccio_A.stl
23.0 x 4.30 x 12.0

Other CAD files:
3D/stl/1xDX_Caviglia_B.stl
3D/stl/1xDX_Gomito_B.stl
3D/stl/1xDX_Avambraccio_B.stl
3D/stl/2xMID_Anca_BTM.stl
3D/stl/1xDX_Anca_A.stl
3D/stl/1xDX_Caviglia_A.stl
3D/stl/1xDX_Gamba_A.stl
3D/stl/1xDX_Ginocchio_B.stl
3D/stl/1xMID_Anca_TOP.stl
3D/stl/38xSP_Cover_1_foro.stl

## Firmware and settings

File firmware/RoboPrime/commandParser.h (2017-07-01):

/**
 * Part of RoboPrime Firmware.
 *
 * commandParser.h
 * Serial command interpreter.
 * 
 * RoboPrime Firmware, (https://github.com/simonepri/RoboPrime)
 * Copyright (c) 2015, Simone Primarosa, (https://simoneprimarosa.com)
 *
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
 * @copyright     Copyright (c) 2015, Simone Primarosa, (https://simoneprimarosa.com)
 * @link          (https://github.com/simonepri/RoboPrime)
 * @since         0.0.0
 * @require       bodyMovement, animationStore
 * @license       MIT License (https://opensource.org/licenses/MIT)
 */
 
/*
 * PURPOSE:
 *
 * This create a class to manage and interpret the incoming serial messages.
 *
 * Implemented S codes:
 * S0 - Set the default angle for a servo.
 * S1 - Set a angle width for a servo.
 * S2 - Sweep to an angle for a servo.
 * S3 - Apply an animation.
 *
 * Implemented Q codes:
 * Q0 - Plan a movment for a servo.
 *
 * Implemented C codes:
 * C0 - Calibrate servo bound.
 */
 
#ifndef _COMMAND_PARSER_H
#define _COMMAND_PARSER_H

#define SERIAL_BAUD         115200
#define DEFAULT_CMD_IDX        255
#define DEFAULT_CODE_VALUE   65535

#define numIdx(num) num-'0'
#define alpIdx(chr) chr-'A'
#define usedCode(val) (val != DEFAULT_CODE_VALUE)

#define _A_ alpIdx('A')
#define _B_ alpIdx('B')
#define _C_ alpIdx('C')
#define _D_ alpIdx('D')
#define _E_ alpIdx('E')
#define _F_ alpIdx('F')
#define _G_ alpIdx('G')
#define _H_ alpIdx('H')
#define _I_ alpIdx('I')
#define _J_ alpIdx('J')
#define _K_ alpIdx('K')
#define _L_ alpIdx('L')
#define _M_ alpIdx('M')
#define _N_ alpIdx('N')
#define _O_ alpIdx('O')
#define _P_ alpIdx('P')
#define _Q_ alpIdx('Q')
#define _R_ alpIdx('R')
#define _S_ alpIdx('S')
#define _T_ alpIdx('T')
#define _U_ alpIdx('U')
#define _V_ alpIdx('V')
#define _W_ alpIdx('W')
#define _X_ alpIdx('X')
#define _Y_ alpIdx('Y')
#define _Z_ alpIdx('Z')

struct cmd_t {
  bool isBusy;
  uint8_t firstCode, activeCode;
  uint16_t valueCode[_Z_ + 1];
};

class CommandParser {
  public:
    static void begin();
    static void parseSerial();
  private:
    // No-one have to create an istance of this class as we use it as
    // a singleton, so we keep constructor as private.
    CommandParser();
    
    static void parseByte(char _b);
    static void parseCode();
    
    static void parseCodeS();
    static void parseCodeS0();
    static void parseCodeS1();
    static void parseCodeS2();
    static void parseCodeS3();
    
    static void parseCodeQ();
    static void parseCodeQ0();
    static void parseCodeQ1();
    
    static void parseCodeC();
    static void parseCodeC0();
    
    static cmd_t parser;
};

#endif

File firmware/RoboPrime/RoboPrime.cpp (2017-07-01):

/**
 * Part of RoboPrime Firmware.
 *
 * main.cpp
 * Setup for library and main loop.
 * 
 * RoboPrime Firmware, (https://github.com/simonepri/RoboPrime)
 * Copyright (c) 2015, Simone Primarosa, (https://simoneprimarosa.com)
 *
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
 * @copyright     Copyright (c) 2015, Simone Primarosa, (https://simoneprimarosa.com)
 * @link          (https://github.com/simonepri/RoboPrime)
 * @since         0.0.0
 * @require       SerialServo
 * @license       MIT License (https://opensource.org/licenses/MIT)
 */
 
#include "Arduino.h"
#include "serialServo.h"
#include "bodyMovement.h"
#include "commandParser.h"
#include "animationStore.h"

void setup() {
  Serial.begin(SERIAL_BAUD);
  SerialServo::begin();
  BodyMovement::begin();
  AnimationStore::begin();
  CommandParser::begin();
}

void loop() {
  /*static uint32_t _time;
  uint32_t _time2 = micros();
  Serial.println(_time2-_time);
  _time = _time2;*/
  SerialServo::servoRoutine();
  BodyMovement::movementPlanner();
  AnimationStore::executeAnimation();
  CommandParser::parseSerial();
}

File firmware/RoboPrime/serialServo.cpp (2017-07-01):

 /**
 * Part of RoboPrime Firmware.
 *
 * serialServo.cpp
 * Interrupt driven Serial Servo library for Arduino using 4017 Counter IC.
 *
 * RoboPrime Firmware, (https://github.com/simonepri/RoboPrime)
 * Copyright (c) 2015, Simone Primarosa, (https://simoneprimarosa.com)
 *
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
 * @copyright     Copyright (c) 2015, Simone Primarosa, (https://simoneprimarosa.com)
 * @link          (https://github.com/simonepri/RoboPrime)
 * @since         0.0.0
 * @license       MIT License (https://opensource.org/licenses/MIT)
 */

#include "Arduino.h"
#include "serialServo.h"
/**
 * "sequence" variable is located in SRAM momery and is a flag in order to enable
 * time compensation for a squence of movments.
 */
bool
  SerialServo::sequence;

/**
 * "channel" variable is located in SRAM momery and store the next channel that
 * will be uptated in the Interrupt Routine Service.
 */
volatile uint16_t 
  SerialServo::channel[SERIAL_SERVO_BANKS];
  
/**
 * "period" variable is located in SRAM momery and store the time elapsed from
 * the last update of a channel.
 */
volatile uint16_t 
  SerialServo::period[SERIAL_SERVO_BANKS];
  
/**
 * "data" array is located in SRAM momery and store information about the setted
 * pulse width for each channel.
 */
servo_data_t
  SerialServo::data[SERIAL_SERVO_CHANNELS];

/**
 * "bound" array is located in FLASH memory and store information about the maximum
 * and minimum pulse width that can be setted for each channel.
 */
const PROGMEM uint16_t
  SerialServo::bound[SERIAL_SERVO_CHANNELS][BOUND_SIZE] = SERVO_WIDTH_BOUND;

/**
 * Initializes class's fields.
 * It programs each pin as an OUTPUT pin.
 * It sends a reset pulse to the 4017
 * It starts Timer1 interrupt.
 */
void SerialServo::begin() {
  for(uint8_t _ch = 0; _ch < SERIAL_SERVO_CHANNELS; _ch++) {
    data[_ch].pulseReached = true;
    data[_ch].updateDisabled = true;
    data[_ch].incrementTicks = 0;
    data[_ch].eachusTicks = 0;
    data[_ch].pulseTicks = 0;
    data[_ch].lastUpdate = 0;
    data[_ch].actionTicks = 0;
  }
  period[SERIAL_SERVO_BANKA] = 0;
  period[SERIAL_SERVO_BANKB] = 0;
  channel[SERIAL_SERVO_BANKA] = SERIAL_SERVO_BANKA_LOW;
  channel[SERIAL_SERVO_BANKB] = SERIAL_SERVO_BANKB_LOW;
  
  // Set the pins we will use for Bank A (OCR1A) as outputs and pulse reset.
  pinMode(BANKA_PULSE_PIN,OUTPUT); 
  pinMode(BANKA_RST_PIN,OUTPUT);
  digitalWrite(BANKA_RST_PIN,HIGH);
  digitalWrite(BANKA_RST_PIN,LOW);
  // Set the pins we will use for Bank B (OCR1B) as outputs and pulse reset.
  pinMode(BANKB_PULSE_PIN,OUTPUT); 
  pinMode(BANKB_RST_PIN,OUTPUT);
  digitalWrite(BANKB_RST_PIN,HIGH);
  digitalWrite(BANKB_RST_PIN,LOW);

  TCNT1 = 0;                           // Clear the timer 1 count.
  TCCR1A = 0;                          // Normal counting mode for Timer1.
  TCCR1B = PRESCALER_BITS;             // Set prescaler for Timer1.

  // ENABLE TIMER1 OCR1A INTERRUPT to enabled the first bank (A) of 10 servos.
  TIFR1 |= _BV(OCF1A);                 // Clear any pending interrupts.
  TIMSK1 |=  _BV(OCIE1A);              // Enable the output compare interrupt.

  // ENABLE TIMER1 OCR1B INTERRUPT to enable the second bank (B) of 10 servos.
  TIFR1 |= _BV(OCF1B);                 // Clear any pending interrupts.
  TIMSK1 |=  _BV(OCIE1B);              // Enable the output compare interrupt.

  // Start OCR1A interrupt with an initial delay.
  uint16_t _TCNT1 = TCNT1;
  uint16_t _ticks = msToTicks((START_DELAY_MS));
  OCR1A = _TCNT1 + _ticks;
  _ticks += usToTicks(500);
  // Start OCR1B interrupt with an initial delay.
  OCR1B = _TCNT1 + _ticks;
}

/**
 * Checks if a valid channel is passed.
 *
 * @param _ch channel index.
 * @return false if it's a valid channel, false otherwise.
 */
inline bool SerialServo::isValidChannel(uint8_t _ch) {
  return (_ch < SERIAL_SERVO_CHANNELS);
}

/**
 * Updates a channel to a new pulse width, the class will continue to pulse the
 * channel with this value for the lifetime of the MPU or until writeWidth or
 * writeAngle is called again to update the value.
 *
 * @param _ch channel index.
 * @param _us pulse width to set.
 * @param _inverted if true it reverses the width passed.
 * @param _calibration if true it applies the width without any software adjustment.
 *  It's a special mode used for calibration purposes only.
 */
void SerialServo::writeWidth(uint8_t _ch, uint16_t _us, bool _inverted, bool _calibration) {
  if(!isValidChannel(_ch)) {
    return;
  }
  if(sequence) {
    data[_ch].actionTicks -= TCNT1 - data[_ch].lastUpdate;
  }
  data[_ch].lastUpdate = TCNT1;
  if(!_calibration) {
    _us = raw_validWidth(_ch, _us);
    if(_inverted) {
      _us = raw_invertWidth(_ch, _us);
    }
  }
  raw_writeWidth(_ch, _us);
}

/**
 * Updates a channel to a new angle, the class will continue to pulse the
 * channel with this value for the lifetime of the MPU or until writeWidth or
 * writeAngle is called again to update the value.
 *
 * @param _ch channel index.
 * @param _deg angle to set.
 * @param _inverted if true it reverses the width passed.
 */
void SerialServo::writeAngle(uint8_t _ch, uint16_t _deg, bool _inverted) {
  if(!isValidChannel(_ch)) {
    return;
  }
  if(sequence) {
    data[_ch].actionTicks -= TCNT1 - data[_ch].lastUpdate;
  }
  data[_ch].lastUpdate = TCNT1;
  _deg = raw_validAngle(_ch, _deg);
  if(_inverted) {
    _deg = raw_invertAngle(_ch, _deg);
  }
  _deg = raw_degToUs(_ch, _deg);
  raw_writeWidth(_ch, _deg);
}

/**
 * Reads previously setted pulse width for a channel.
 *
 * @param _ch channel index.
 * @param _inverted if true it reverses the width passed.
 * @return the channel's pulse width.
 */
uint16_t SerialServo::readWidth(uint8_t _ch, bool _inverted) {
  if(!isValidChannel(_ch)) {
    return 0;
  }
  uint16_t _us = raw_readWidth(_ch);
  if(_inverted) {
    _us = raw_invertWidth(_ch, _us);
  }
  return _us;
}

/**
 * Reads previously setted angle for a channel.
 *
 * @param _ch channel index.
 * @param _inverted if true it reverses the width passed.
 * @return the channel's angle.
 */
uint16_t SerialServo::readAngle(uint8_t _ch, bool _inverted) {
  if(!isValidChannel(_ch)) {
    return (uint16_t)-1.0;
  }
  uint16_t _us = raw_readWidth(_ch);
  if(_inverted) {
    _us = raw_invertWidth(_ch, _us);
  }
  return raw_usToDeg(_ch, _us);
}

/**
 * Sets a certain pulse width smoothly for a channel in a predeterminated number
 * of millisecond.
 *
 * @param _ch channel index.
 * @param _us pulse width to set.
 * @param _time time to sweep.
 * @param _inverted if true it reverses the width passed.
 * @return none.
 */
void SerialServo::sweepWidth(uint8_t _ch, uint16_t _us, uint16_t _time,
                             bool _inverted) {
  if(!isValidChannel(_ch)) {
    return;
  }
  if(sequence) {
    data[_ch].actionTicks -= TCNT1 - data[_ch].lastUpdate;
  }
  data[_ch].lastUpdate = TCNT1;
  _us = raw_validWidth(_ch, _us);
  if(_inverted) {
    _us = raw_invertWidth(_ch, _us);
  }
  raw_sweepWidth(_ch, _us, _time);
}
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

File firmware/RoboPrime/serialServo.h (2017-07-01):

 /**
 * Part of RoboPrime Firmware.
 *
 * serialServo.cpp
 * Interrupt driven Serial Servo library for Arduino using 4017 Counter IC.
 *
 * RoboPrime Firmware, (https://github.com/simonepri/RoboPrime)
 * Copyright (c) 2015, Simone Primarosa, (https://simoneprimarosa.com)
 *
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
 * @copyright     Copyright (c) 2015, Simone Primarosa, (https://simoneprimarosa.com)
 * @link          (https://github.com/simonepri/RoboPrime)
 * @since         0.0.0
 * @license       MIT License (https://opensource.org/licenses/MIT)
 */
 
/*
 * PURPOSE:
 *
 * The library uses two 4017 Counter IC to generate pulses to independently
 * drive up to 20 servos (10 servos for each 4017) from four Arduino Pins.
 * 
 * The interrupt are based on Timer1 output compare register A and Timer1 output compare register B:
 *  - OCR1A is linked to digital pin 9 and so we use digital pin 9 to
 *    generate the clock signal for the first 4017 counter (Bank A).
 *  - Pin 12 is used as the reset pin for the first 4017 counter (Bank A).
 * 
 *  - OCR1B is linked to digital pin 10 and so we use digital pin 10 to
 *    generate the clock signalfor the second 4017 counter (Bank B).
 *  - Pin 13 is used as the reset pin for the second 4017 counter (Bank B).
 * 
 * Thanks to DuaneB for the idea of using 4017.
 */

#ifndef _SERIAL_SERVO_H
#define _SERIAL_SERVO_H

#define SERIAL_SERVO_BANKA_LOW      0     // Bank A lower-bound index.
#define SERIAL_SERVO_BANKA_UP       9     // Bank A upper-bound index.
#define SERIAL_SERVO_BANKB_LOW     10     // Bank A lower-bound index.
#define SERIAL_SERVO_BANKB_UP      19     // Bank A upper-bound index.
#define SERIAL_SERVO_CHANNELS      20     // Number of channels.

#define SERIAL_SERVO_BANKS          2
#define SERIAL_SERVO_BANKA          0
#define SERIAL_SERVO_BANKB          1

#define BANKA_PULSE_PIN             9
#define BANKA_RST_PIN              12
#define BANKB_PULSE_PIN            10
#define BANKB_RST_PIN              13

#define PRESCALER_BITS              2     // 010.
#define PRESCALER_VALUE             8     // Timer1 prescaler. 8 = 2 ticks = 1us. (With 16MHz clock)
#define START_DELAY_MS              2     // Initial delay for interrupt start.

#define MIN_SERVO_ANGLE             0
#define MAX_SERVO_ANGLE          1800     //180*10

#define BOUND_MIN 0
#define BOUND_MAX 1
#define BOUND_SIZE 2

#define SERVO_WIDTH_BOUND {                                                    \
  {550, 2200}, {480, 2100}, {640, 2360}, {560, 2260}, {580, 2200},             \
  {600, 2260}, {550, 2300}, {630, 2220}, {650, 2280}, {750, 2440},             \
  {590, 2300}, {650, 2350}, {640, 2630}, {610, 2370}, {520, 2250},             \
  {600, 2190}, {590, 2270}, {520, 2100}, {550, 2220}, {720, 2230}              \
}

#define ticksToUs(ticks)     ((ticks) >> 1)        // ((_ticks * PRESCALER_VALUE)/ clockCyclesPerMicrosecond())
#define usToTicks(us)        ((us) << 1)
#define msToTicks(ms)        (usToTicks(uint32_t(ms)) * 1000)
#define ticksToMs(ticks)     (ticksToUs(ticks) / 1000)

#define fastMsToTicks(ms)        (usToTicks(ms) << 10)
#define fastTicksToMs(ticks)     (ticksToUs(ticks) >> 10)

#define PORTB_PIN(_pin) (1 << (_pin-8))

struct servo_data_t {
  bool pulseReached;
  float eachusTicks;
  uint16_t lastUpdate;
  int32_t actionTicks;
  volatile bool updateDisabled;
  volatile int16_t deltaTicks;
  volatile float incrementTicks;
  volatile uint16_t pulseTicks;
};
    
class SerialServo {
  public:
    static void begin();

    static bool isValidChannel(uint8_t _ch);
    static void writeWidth(uint8_t _ch, uint16_t _us, bool _inverted = false, bool _calibration = false);
    static void writeAngle(uint8_t _ch, uint16_t _deg, bool _inverted = false);
    static uint16_t readWidth(uint8_t _ch, bool _inverted = false);
    static uint16_t readAngle(uint8_t _ch, bool _inverted = false);
    static void sweepWidth(uint8_t _ch, uint16_t _us, uint16_t _time,
                           bool _inverted = false);
    static void sweepAngle(uint8_t _ch, uint16_t _deg, uint16_t _time,
                           bool _inverted = false);
    static void wait(uint8_t _ch, uint16_t _time);
    static uint16_t readMinWidth(uint8_t _ch, bool _inverted = false);
    static uint16_t readMaxWidth(uint8_t _ch, bool _inverted = false);
    static bool isMoving(uint8_t _ch);
    static void enableSequence();
    static void disableSequence();
    
    static void servoRoutine();
    
    static void OCR1A_ISR();
    static void OCR1B_ISR();
  private:
    // No-one have to create an istance of this class as we use it as
    // a singleton, so we keep constructor as private.
    SerialServo();

    // All raw_ function declared here do not check the validity of the passed
    // arguments for speed reasons. They are supposed to be used only internally.
    
    static uint16_t raw_degToUs(const uint8_t &_ch, const uint16_t &_deg);
    static uint16_t raw_usToDeg(const uint8_t &_ch, const uint16_t &_us);
    static uint16_t raw_validWidth(const uint8_t &_ch, const uint16_t &_us);
    static uint16_t raw_validAngle(const uint8_t &_ch, const uint16_t &_deg);
    static uint16_t raw_invertWidth(const uint8_t &_ch, const uint16_t &_us);
    static uint16_t raw_invertAngle(const uint8_t &_ch, const uint16_t &_deg);
    
    static void raw_writeWidth(const uint8_t &_ch, const uint16_t &_us);
    static uint16_t raw_readWidth(const uint8_t &_ch);
    static void raw_sweepWidth(const uint8_t &_ch, const uint16_t &_us,
                               const uint16_t &_time);
    static void raw_wait(const uint8_t &_ch, const uint16_t &_time);
    static uint16_t raw_readMinWidth(const uint8_t &_ch);
    static uint16_t raw_readMaxWidth(const uint8_t &_ch);
    
    static void raw_movementCheck();
    static void raw_incrementCalculator();
    
    static bool sequence;
    static volatile uint16_t channel[SERIAL_SERVO_BANKS];
    static volatile uint16_t period[SERIAL_SERVO_BANKS];
    static servo_data_t data[SERIAL_SERVO_CHANNELS];
    static const PROGMEM uint16_t bound[SERIAL_SERVO_CHANNELS][BOUND_SIZE];
};

#endif

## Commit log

2017-07-01 Fix multi-character character constant
    [commandParser.cpp]
2017-07-02 Add orcad schematics
    [ROBOT.DSN]
2017-07-02 Add original fritzing schematics
    [Umanoide Sketch.fzz, components.fzz]
2017-07-02 Remove camera from schematics
    [Umanoide Sketch.fzz, components.fzz]
2017-07-02 Add exported stl
    [1xDX_Anca_A.stl, 1xDX_Anca_B.stl, 1xDX_Anca_BT.stl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]
2017-07-05 Rename a 3d model
    [2xMID_Anca_BTM.stl]
2017-07-06 Add stl thumbnails
2017-07-06 Update shematics
    [Umanoide Sketch.fzz]

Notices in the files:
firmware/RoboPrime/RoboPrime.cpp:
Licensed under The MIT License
